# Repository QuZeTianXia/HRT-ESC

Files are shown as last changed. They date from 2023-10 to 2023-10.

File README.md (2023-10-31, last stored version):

# 更新日志      
(https://img.tg/image/O1jPRb)   
+2023/10/31/20:21   
赛前能用的四轮加压版本，但后轮还是会跳动，而且加压速率较慢。 
+ 2023/10/15/9:35  
梳理了逻辑，增加了使用CAN改变加压力度配制参数的功能。  
	+ Data[0] = 0xAA ---> Data[1] = Quick_Accelerate;  
	+ Data[0] = 0xBB ---> Data[1] = Slow_Accelerate;   
下一步计划增加P控制
+ 2023/10/13/21:34  
更新了23D四轮制动的版本，但未经测试。
+ 2023/10/13/21:25   
更新了23D刚刚可用的只有前轮制动的版本。

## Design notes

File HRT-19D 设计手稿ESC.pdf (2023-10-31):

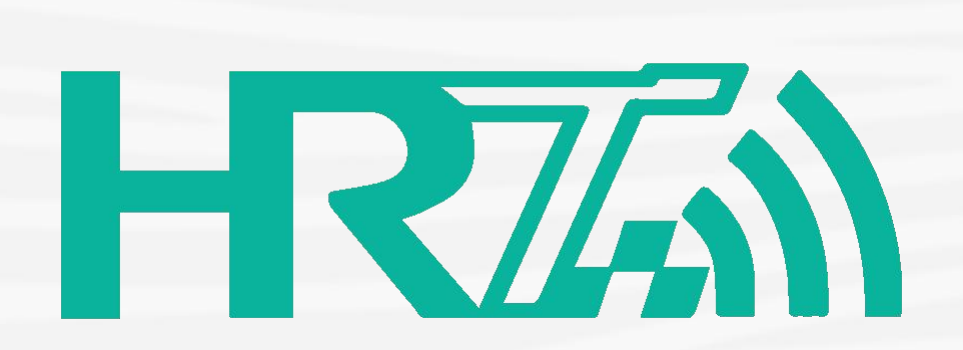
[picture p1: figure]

## Season 2019

## ESC 设计手稿

## Department of ESC

## 设计者： 卢奇麟 王书鹏 赵砚秋 等

## Designer: Qilin Lu、Shupeng Wang、Qiuyan Zhaoetc. 关键词： 稳定、快速响应、轻量化

## Keywords: Reliable, Rapid response, Light-weight

目录

## 1. ESC 功能

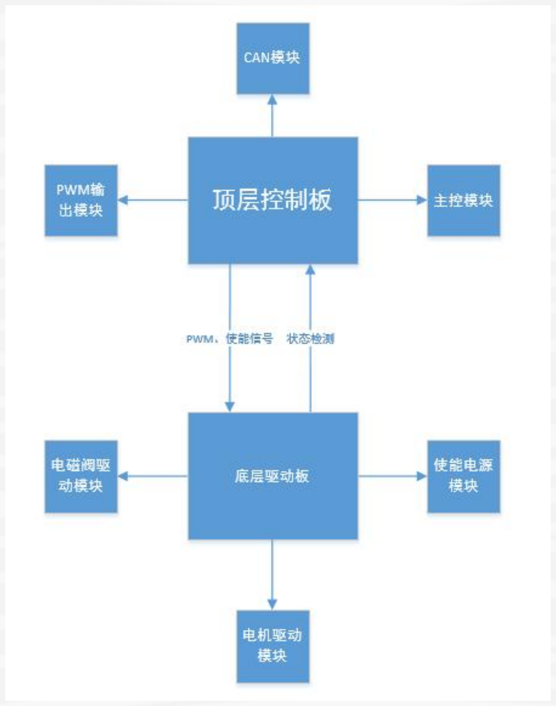
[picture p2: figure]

图 1-1 ESC 功能模块构成
ESC 全名为 Electronic Stability Control，一般用于控制车身高速行驶状态下的的稳定性。 今年车队研发 ESC 主要用于制动，实现对四个车轮稳定而准确可控的油压控制。
如图 1-1 所示，ESC 主要由两个部分构成：底层的驱动板以及顶层的控制板。其中顶层 控制板涉及到收发 CAN 信号，主控算法以及 PWM 输出三大部分；底层的驱动板主要涉及电 磁阀，电机的驱动以及电源使能模块，这些部分会在后文详细介绍。
由于 ESC 制动力不足，并不适合用于紧急制动，所以在功能上只是作为制动的冗余系统 以及检测系统，在进入 AS Ready 前以及实际 EBS 制动时检测油压，如果油压没有在规定时 间内（3s）增长到一定程度，就认为 EBS 错误，自动制动并发出代表错误的信号。另外在无 人跑动直线时，车辆需要缓停，制动力也由 ESC 提供。

## 2. 针对规则

3.2.4. 在 AS 切换至“AS Ready”前，必须存在一个初始状态检查来保证 EBS 和它的冗余系 统可以像期望的一样建立制动压力。
3.2.5. 驱动系统不被认为成制动系统。
3.2.6. 如果确保存在双向监测，行车制动可以认为是一套冗余系统。

## 3. 关联信号模块

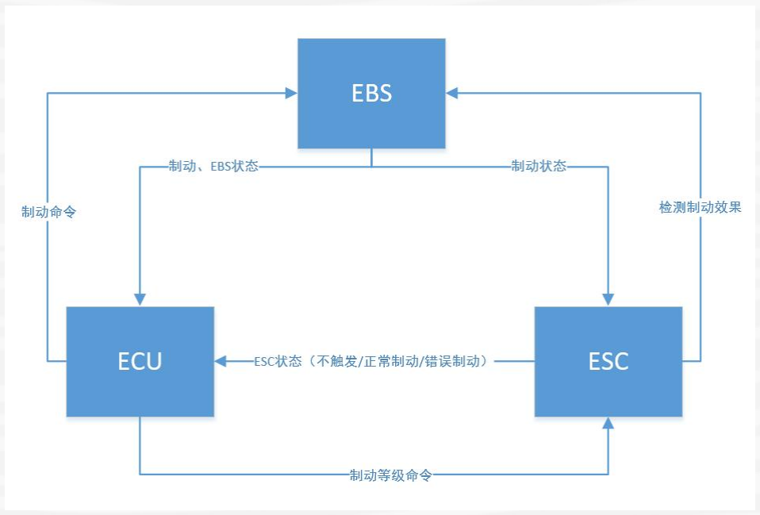
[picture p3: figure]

图 3-1 ESC 与整车信号交流示意图

如图 3-1 所示，ESC 主要与 EBS 和 ECU 有信号交流。其中 ECU 会向 ESC 发送 0-5 的制动 等级信号，分别对应油压 0 到 1Mpa。接收信号后，ESC 内部自带的电机转动（占空比 0.6-0。 9），并通过开闭电磁阀实现油路转换与油压调节，确保目标油压可以保持在一定范围内。同 时 ESC 也会自检油压，并发送自身的状态位。
ESC 会接收 EBS 的制动状态，并检测 EBS 是否正常制动。如果 EBS 制动后规定时间内没 有足够的油压，ESC 会自动补位，同时发送 EBS 的错误位。该错误状态会被锁存直到检测到 EBS 的状态不再是制动状态。
进入 AS Ready 状态前，ESC 会先进行制动，检测油压正常后，进入无人模式，EBS 触发。 如果 ESC 检测正常，则可以进入 AS Ready 状态，否则 ESC 报错，系统退出 AS Ready 状态。

## 4. 最终电路设计

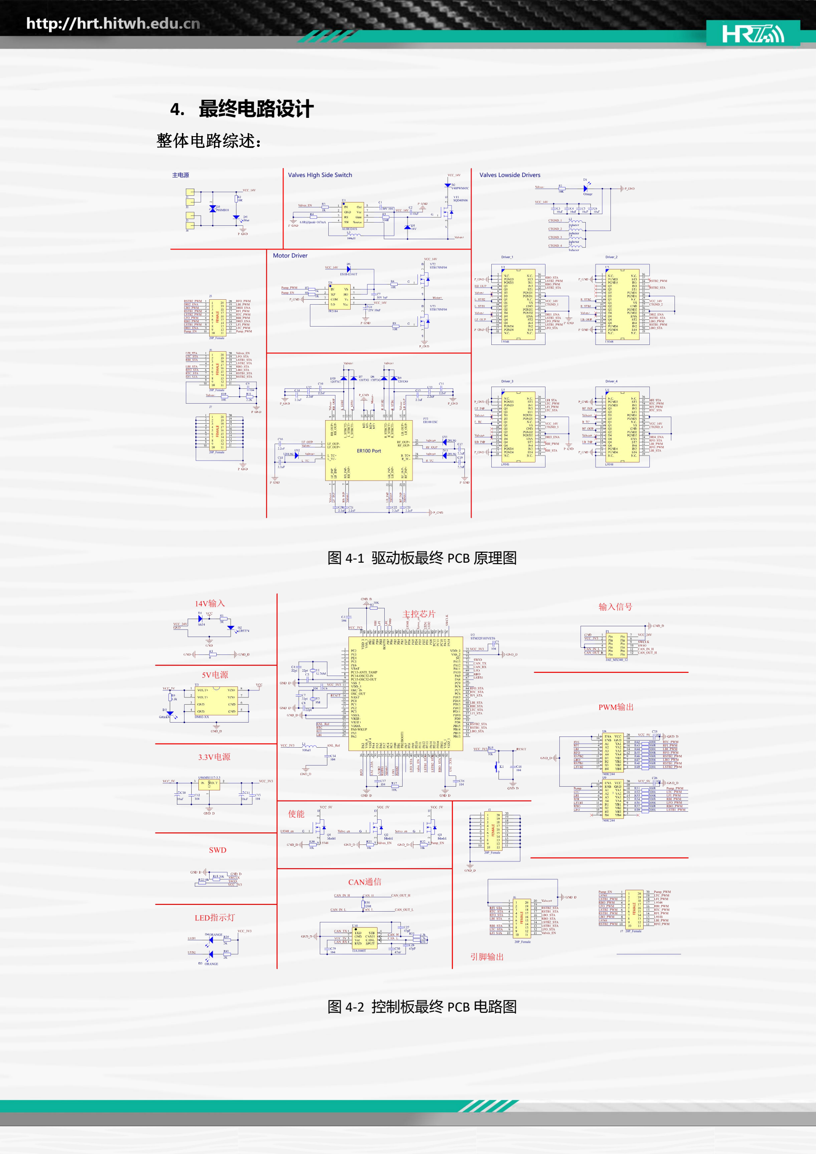
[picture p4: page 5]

整体电路综述：

图 4-1 驱动板最终 PCB 原理图

图 4-2 控制板最终 PCB 电路图

接下来介绍两个板子的主要构成部分，至于 LED、SWD 等不再赘述。 驱动板：

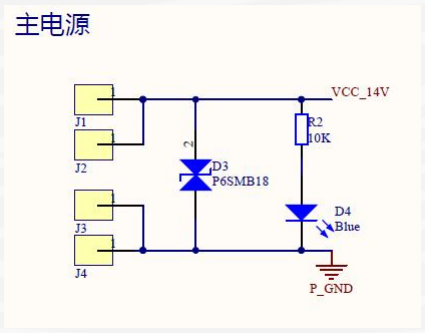
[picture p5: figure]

图 4-3 电源输入
由于电机的额定电压在 14V,为了避免电压过高损坏电机的问题，采用铝壳电源将低压 电 24V 转化为 14V 电源，驱动电机及电磁阀。该电流最大时可达 9A,铝壳电源最大电流 13A， 符合要求。
电路在接通、断开电感负载或大型负载时常常会产生很高的操作过电压，这种瞬时过电 压称为浪涌电压，是一种瞬变干扰。而电磁阀和电机都是大功率电感元件，在通断过程中即 便采用二级管泄压，难免会产生瞬时的过电压。P6SMB18 是一种双向瞬态二极管，在电压 超过 16.2V 时，可以瞬时导通以避免该部分电流损坏电路系统。

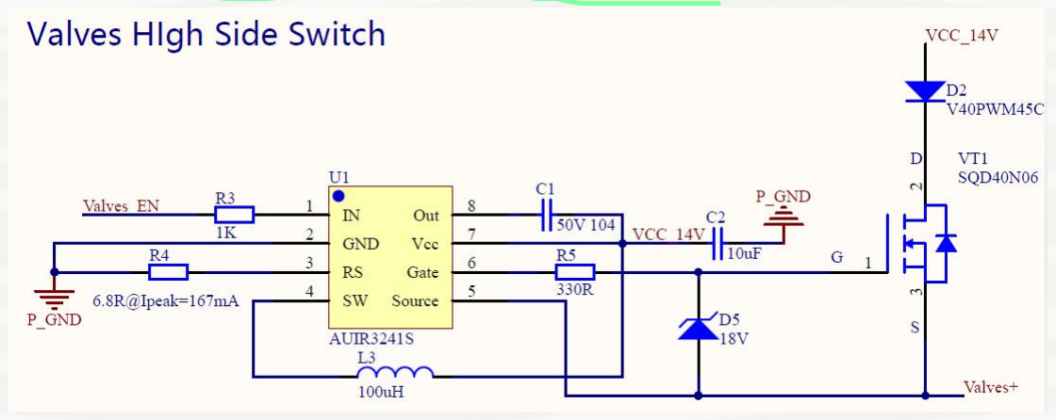
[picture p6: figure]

图 4-4 驱动板电源使能
该应用电路通过输入引脚 IN 实现对 Gate 开关的控制，进而控制整个电源的通断。 AUIR3241 是宽电压供电的大功率电源控制芯片，其供电电压可以为 3-36V 的任意值， 输入端的电压可以在 2.5-5V 之间实现整个电源电路的通断，可以兼容单片机 3.3V。 使用大功率 mos 管 SQD40N06 流经所有的电源电压,可承受 40A 的电流，完全符合系统的 要求(电磁阀部分最大约 6A)。

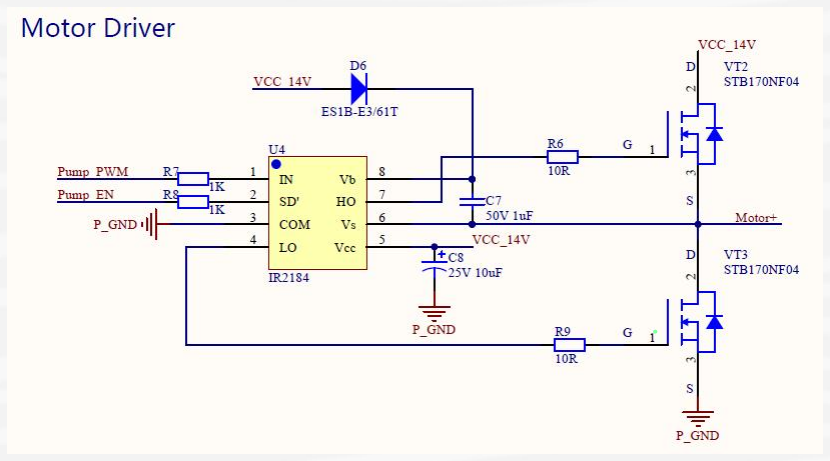
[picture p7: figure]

图 4-5 电机控制电路
该电路用于控制电机的停转。由于电机属于感性负载，其上的电流不能突变，不能直接 使用 PWM 控制二极管通断供电。IR184 是一种半桥功率放大芯片，可以通过两路相反的输 出分别控制电源和 GND 的通断，从而实现 PWM 直接控制电机的功能。
IR2184 的输入部分包括使能和 PWM。使能信号为低时，输出部分 HO 与 LO 都为低；否 则根据 IN 引脚的输入，HO 与 LO 输出相反。驱动电机的部分为典型的自举电路：IN 输入为 低时，LO 为高，Motor 和 GND 导通，此时电容 C7 由电源电压开始充电；IN 输入为高时， LO 为低，HO 的电压等于 Vb 的电压。MOS 管在 Vgs 达到一定压差时才会导通，因此 HO 与 Motor 上的压差等于电容电压，Motor 此时为高。如此充放电周而复始，实现 PWM 控制电 机转动的目的。
在实际测试的过程中，1uF 的电容在 PWM 频率为 1000HZ，占空比 0.7 时由于存储的电 荷不足，mos 管的 Vgs 达不到阈值，电机直接连接到 Vs 引脚。由于电机的电流不能突变， 过剩的电流击穿了 Vs 与 HO 之间的 mos 管，芯片损坏，后来换成 10uF 的电容，不再出现芯 片损坏的问题。

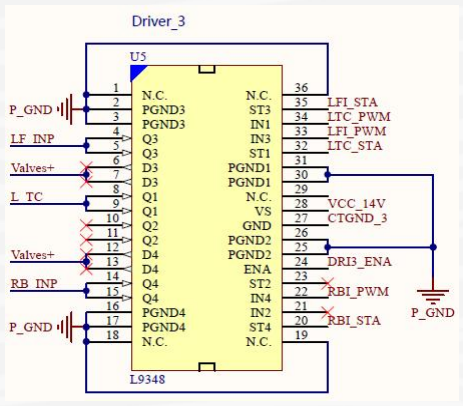
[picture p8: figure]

图 4-6 电磁阀驱动电路（一）

如图 4-6，电磁阀驱动电路使用 L9348 芯片，每一个芯片可以分别输出四路独立的 PWM，对应四个电磁阀开关控制。实际电磁阀数量为 14 个，共使用 4 个 L9348 芯片。 L9348 芯片包含四个输入端，4 个状态输出端，4 个电流输出状态（高阻态或导通）， 以及一个总的使能引脚。为了避免麻烦，控制板使用一个引脚控制 4 个芯片的使能。 L9348 本身不具有带动感性负载的能力，但支持 PWM 形式的高速通断，以及最大 3A 的电流导通，相比 1A 可以实现功能的电磁阀，电流输出要求可以满足。此外，该芯片可以 检测错误状态，包括输出过载、过温等。输出脚和输入脚在正常情况下会保持一致，（超过 667Hz 的输入会导致输出一直为高），发生错误后状态反转，所以可以输出电流时检测输出 状态，为低时报错。
另外，每个芯片的 VCC 和 GND 都有电容和电感滤波，不再单独截图。

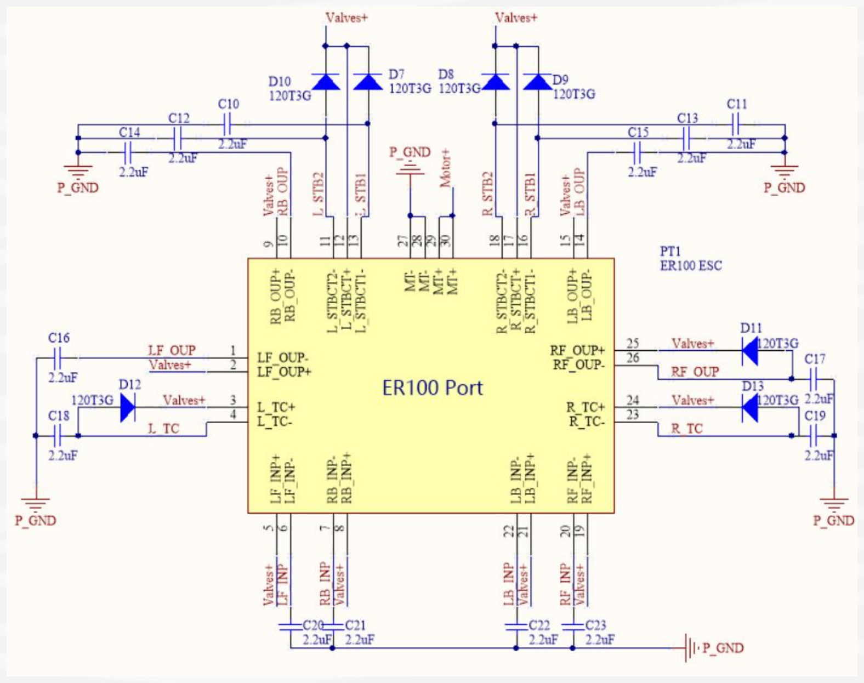
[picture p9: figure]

图 4-7 电磁阀驱动电路（二）

ER100Port 实际代表与电磁阀位置对应的过孔，实际通过焊线连接二者。L9348 的输出 代表与地导通与否，因此在导通且电源使能后，可以控制 PWM 形式的电流流过电磁阀，从 而控制电磁阀导通与否。
120T3G 是一种快速恢复整流二极管，适合实现高频下的通断。PWM 控制电磁阀时，由 于电磁阀为感性负载，其上电流不能突变，这部分电流经过 123T3G 二极管进入 Valve 电源 端，避免损伤 L9348 芯片。

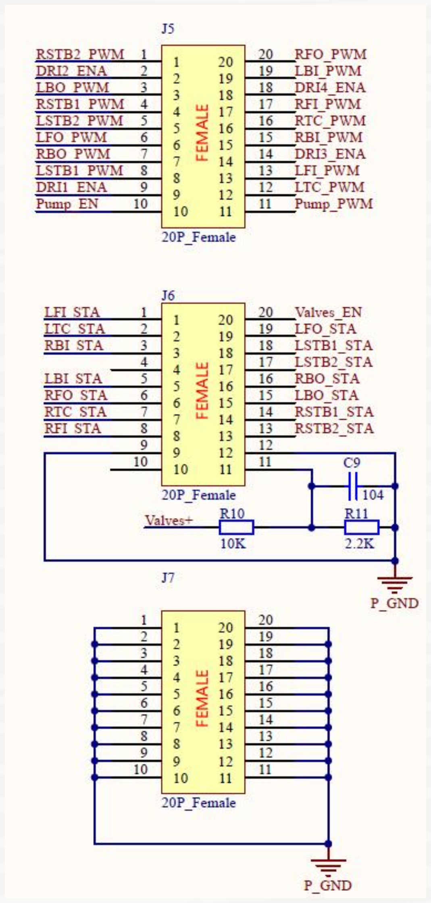
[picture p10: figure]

图 4-8 驱动板控制板连接

使用 Female 板对板连接器连接驱动板与控制板，同时固定二者之间的位置。信号包含 15 路 PWM，4 个 L9348 使能信号，1 个电机使能信号，1 个电源使能信号，1 个电源 ADC 信号采集口，以及 14 个状态位。

控制板：

控制板主要实现接收信号、中央控制、PWM 算法三个部分。

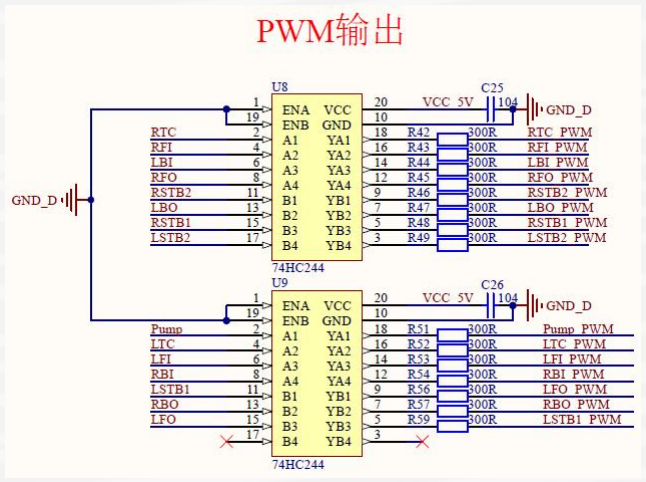
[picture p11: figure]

图 4-9 PWM 输出

一共有 14 个需要控制的电磁阀，再加上电机，实际共输出 15 路 PWM，分别由 4 路定 时器输出 PWM 。

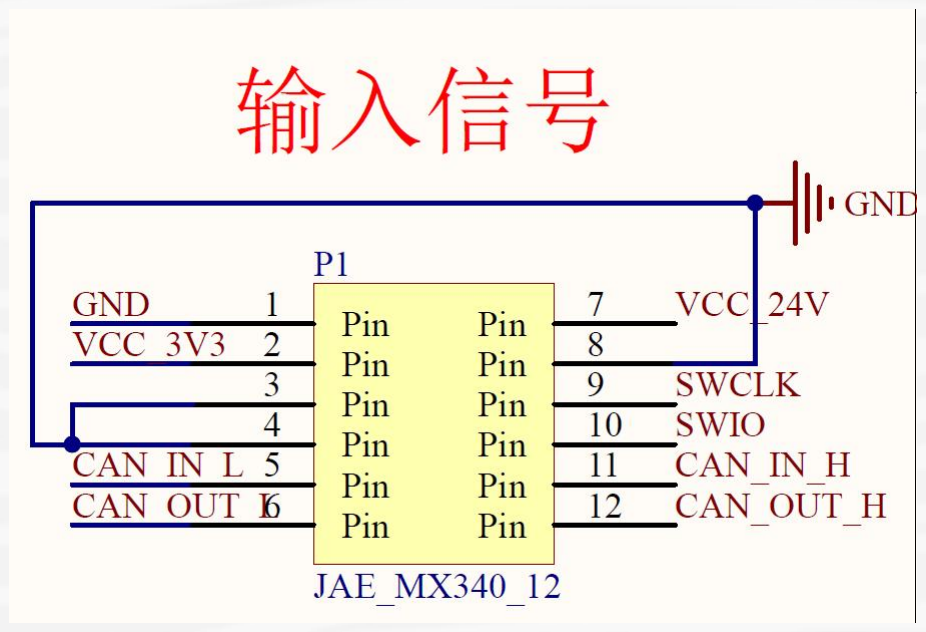
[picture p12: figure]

图 4-10 控制板的输入信号

输入信号较少，只有电源、CAN、SWD 下载口三个部分，获取整车状态以及和 EBS 双向通信都通过 CAN 通信。

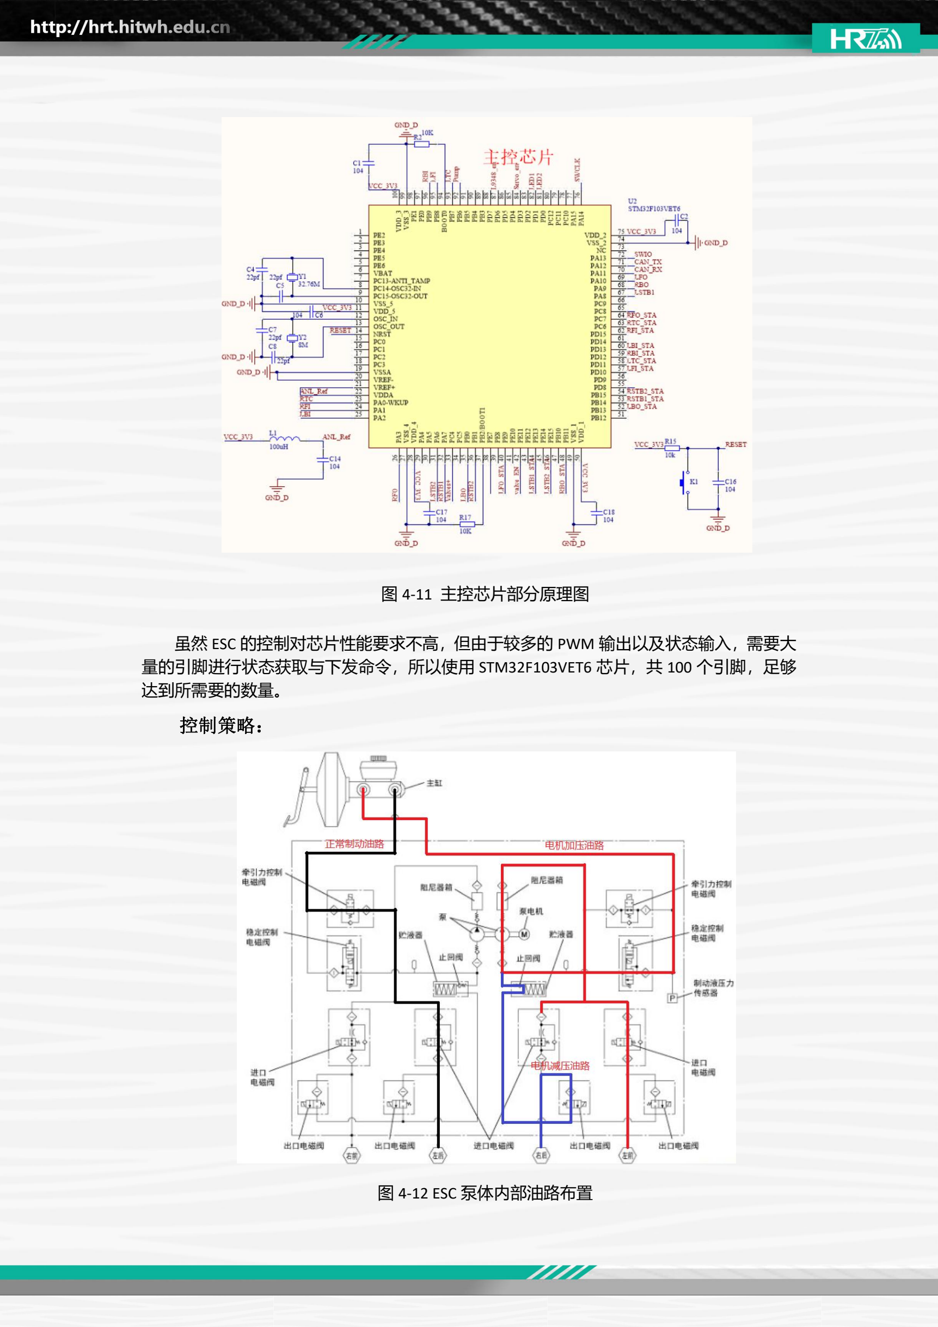
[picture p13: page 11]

图 4-11 主控芯片部分原理图

虽然 ESC 的控制对芯片性能要求不高，但由于较多的 PWM 输出以及状态输入，需要大 量的引脚进行状态获取与下发命令，所以使用 STM32F103VET6 芯片，共 100 个引脚，足够 达到所需要的数量。 控制策略：

图 4-12 ESC 泵体内部油路布置

| 进口电磁阀 | 出口电磁阀 | 牵引力控制电 磁阀 | 稳定性控制 电磁阀 | 电机
增压 | 不通电/ON | 不通电/OFF | 通电/ON | 通电/OFF | 转
降压 | 通电/OFF | 通电/ON | 不通电/OFF | 不通电/ON | 转
保压 | 通电/OFF | 不通电/OFF | 不通电/OFF | 不通电/ON | 不转
表 4-1 不同功能下电磁阀通断情况
如图 4-12 所示，ESC 使用电机进行加减压的过程实际就是改变制动油流动的路径以及电 机转动的 PWM 占空比。通过控制板输出 PWM 可以改变电磁阀开关状态，进而实现改变油 路的目的。
表 4-1 是具体实现修改油路的电磁阀通断表。当所有的电磁阀都不通电时，有人状态可 以正常的踩动加压，其油路由图 4-10 黑色线所示；要实现某一路增压，需要通电牵引力电 磁阀与稳定控制电磁阀，油路为图 4-10 的红色线所示，电机转动即可带动制动油流向轮边； 需要减压时，通电进口电磁阀与出口电磁阀，制动油沿着图 4-10 蓝线所示到达储液器；要 实现保压的目的，只需要通电进口电磁阀即可。
实际测试过程中发现，进口电磁阀可以基本保证油压不增加，但存在漏油现象，为了减 小该现象，实际控制时电机一直处于转动状态，也可以避免电机频繁停转对系统的冲击。

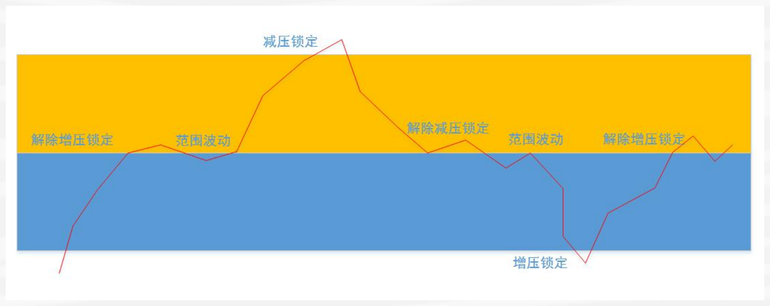
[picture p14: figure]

图 4-13 控制策略示意图
相比机械式的气瓶制动，ESC 的制动力明显不足，最大约 1MPa，不可能实现制动测试。 但 ESC 的优势在于可以实时监测控制各个车轮的油压，以达到制动力最优分配的目的。 ESC 控制油压时，系统总处于加压、减压、保压之一的状态，而状态之间切换的过程需 要一定时间并产生峰值电压，对系统不利。所以基本的控制策略如图 4-13 所示，分别设定 一个合适的上下阈值（中间值为目标油压），检测到油压波动超过设定的范围后，设置锁存 位，系统进入加压或降压的状态直到油压重新回到目标值。 实际测试时，关闭进口电磁阀油压整体有下降的趋势；为了避免测量油压时数据波动导 致的频繁状态转换，上下阈值必须选取与目标值相差较大；但选取过大的偏差，ESC 分配油 压的功能也就失去了意义。经过实际验证，0.08MPa 的阈值偏差为比较好的值。

控制流程

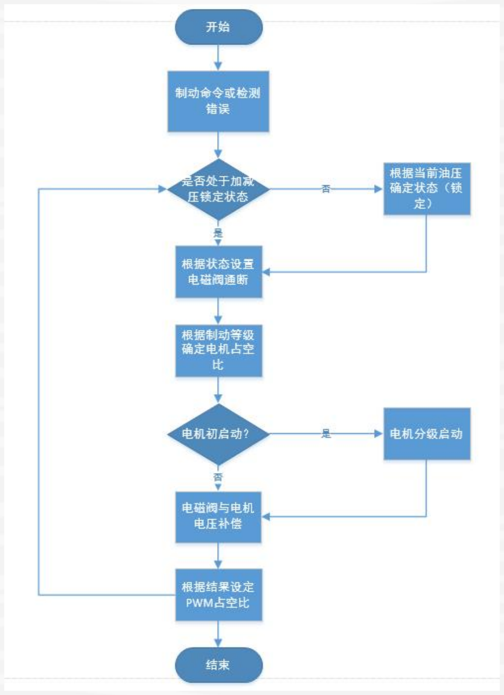
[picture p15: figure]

图 4-14 控制流程示意图

ESC 只在接收到制动命令或者检测到 EBS 制动错误后才会进入制动状态，制动状态控制 流程如图 4-14 所示。进入制动状态后，系统根据置位确定当前的锁定状态，如果没有，则 根据油压和目标值的差确定状态。进入锁定状态后（锁定加压、锁定减压），直到重新达到 目标油压才会停止。
电机的占空比依靠制动等级确定，一般要求电机直接加压时的油压大于目标油压。实际 控制时设定电机与制动等级线性相关，即 1-5 的制动等级对应 0.55-0.95 的电机占空比。 电机的电流与转速关系如下所示：

# Ua = Ce ∗ ∅ ∗ n + I ∗ Ra

所以电机通电时初始转速为零，与之对应的的电流等于 U/R。经过测量，R=3 欧，所以 电机初始启动时的电流非常大，对整个供电系统以及电机都有损害。采取分级启动的方法可 以减小大电流的冲击，即电机刚上电的 1s 内，设定占空比为 0.5+0.5*k（k 为制动等级），待 到电机转速达到一等程度后，再设定目标占空比，可以减小流经电机的冲击电流。 电压补偿可以确保实际的电流（电压/电阻）达到预定值。由于电磁阀（1A）与电机（约 3A）都是比较大电流的器件，难免在电流变化或总量较大时出现电源电压被拉低的情况。 所以需要实时检测电源电压，并根据实际电压按比例补偿占空比，确保电磁阀与电机的实际 电压达到预定值。
控制时序如表 4-2 所示：
Count | ECU | ESC | ESC | 油压采集板
0 | 制动命令 | | | 油压数据
1 | | 设定 PWM | 发送制动状态
2 | | | | 油压数据
3 | 制动命令
4 | | 设定 PWM | 发送制动状态 | 油压数据
5
6 | 制动命令 | | | 油压数据
7 | | 设定 PWM | 发送制动状态
8 | | | | 油压数据
9 | 制动命令
10 | | 设定 PWM | 发送制动状态 | 油压数据
11
12 | 制动命令 | | | 油压数据
13 | | 设定 PWM | 发送制动状态
14 | | | | 油压数据
15 | 制动命令
16 | | 设定 PWM | 发送制动状态 | 油压数据
17
18 | 制动命令 | | | 油压数据
19 | | 设定 PWM | 发送制动状态
20 | | | | 油压数据
30Hz | 10Hz | 10Hz | 10Hz | 15Hz

ECU 以 10Hz 的频率发送制动命令，ESC 也以 10Hz 的频率计算设定 PWM 占空比； 而油压采集信号以 15Hz 的频率获得，高于 ESC 的控制频率，避免数据未更新导致的控制 问题。
油压采集板由一个单独的板子采集，并通过 CAN 信号将采集到的油压发出来。油压采 集板实质为 4 路 ADC 采集板，这里不再赘述。采集到的数据不经处理，以 8 个 CAN 位发 送，每一路油压共 12 位，ESC 需要进行解码获得实际数据。

控制效果

## 5. 传感器选型

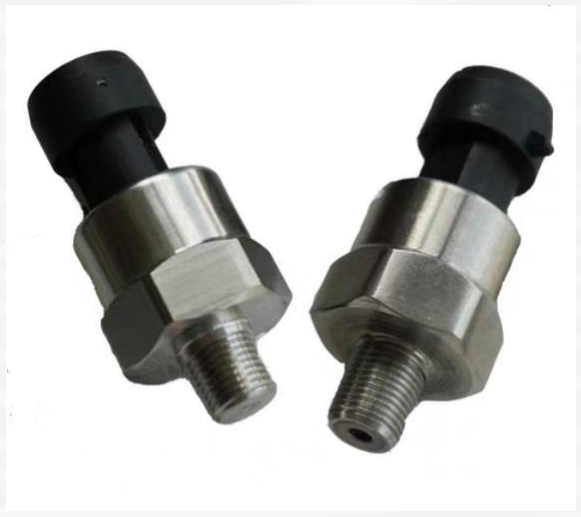
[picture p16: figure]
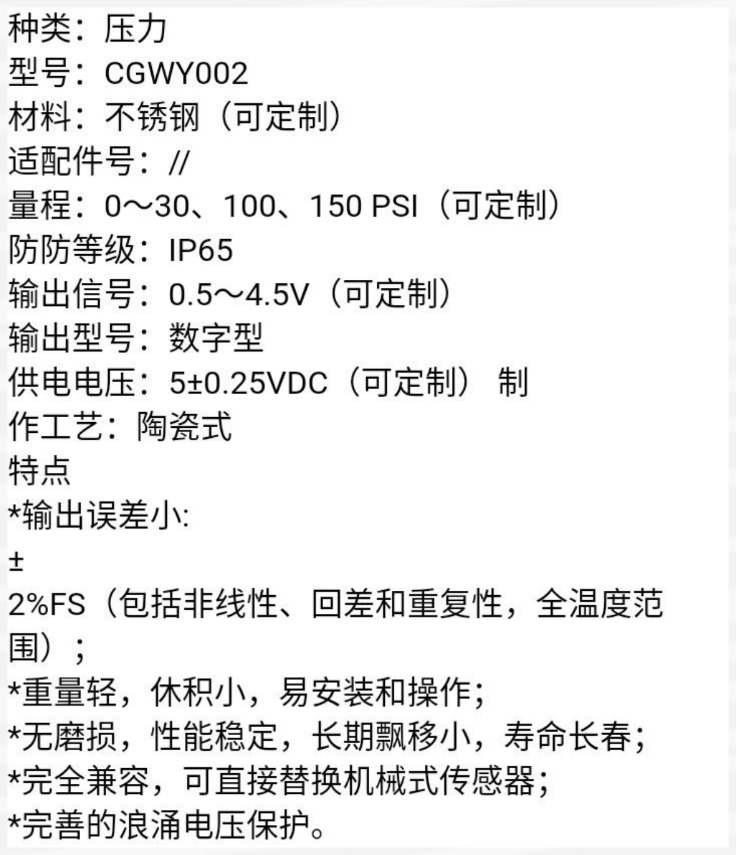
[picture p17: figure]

图 5-1 油压传感器型号

油压传感器定制型号 5V 供电，0.5-4.5V 输出，8MPa 的最大压强测量范围，足够赛车车 轮抱死的油压。

## 6. 安装位置

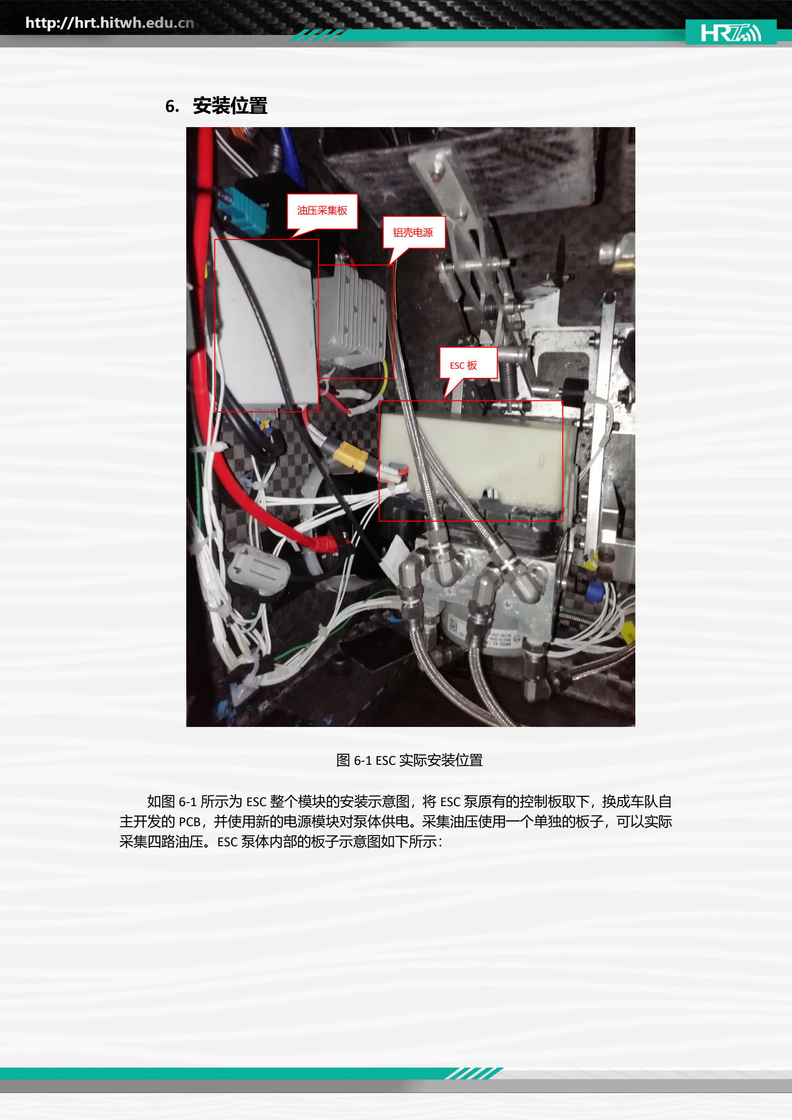
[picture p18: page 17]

图 6-1 ESC 实际安装位置

如图 6-1 所示为 ESC 整个模块的安装示意图，将 ESC 泵原有的控制板取下，换成车队自 主开发的 PCB，并使用新的电源模块对泵体供电。采集油压使用一个单独的板子，可以实际 采集四路油压。ESC 泵体内部的板子示意图如下所示：

铝壳电源

油压采集板

ESC 板

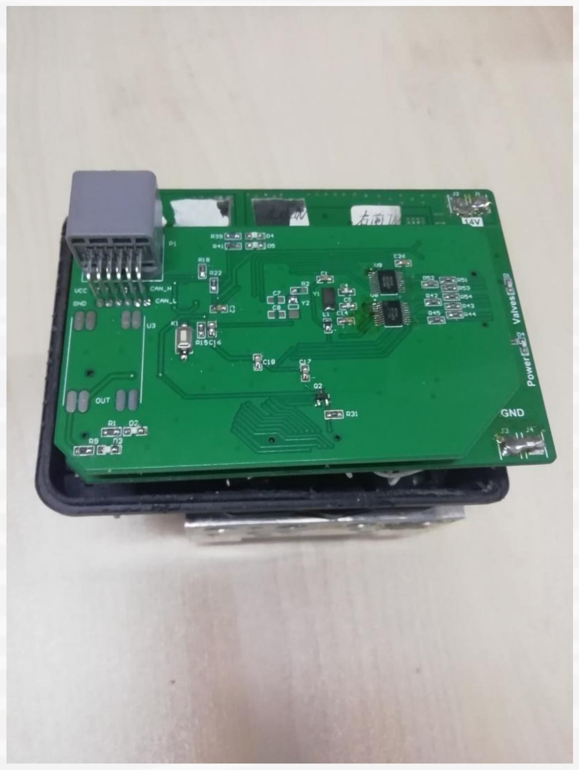
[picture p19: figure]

图 6-2 ESC 内部泵体安装示意图
驱动板与泵体之间通过 MX34 插头连接，电磁阀与电机的的引出脚使用线束焊接，外包 绝缘胶带，再用热熔胶糊上以避免短路。驱动板与控制板之间通过 Female 板对板连接器连 接，在使用热熔胶固定，确保不出现连接松动问题。

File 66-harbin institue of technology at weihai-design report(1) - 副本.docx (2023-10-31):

写在最前面（记得删除）

此为设计手稿模板

今年的模板一是在静态赛答辩时如有需要可以给裁判查阅；二是中国赛或德国赛的设计报告我需要参考每一个系统的设计手稿来写；三是尽可能写的详细些以便后续学弟学妹们关于设计有据可查，不要再发生连着几年设计报告长一样的事情了。

今年因为需要参加国外比赛，所有的内容必须中英文对照，中文在前，英文在后。目录因为word本身的问题所以只能中文/English。

我列的模板大多是以底盘为基本思路，其他系统可以按照自己的设计流程来修改，记得把目录的编号整理好并且及时更新目录

标题和文本的字体已经在模板里列出。

另外关于内容，还是想提醒一下大家多考虑考虑每一个和自己配合或者配合对方的系统，比如悬架要如何考虑空套，应该给空套什么样的设计指导，裁判很喜欢问这种问题

同时，国外有很多非常优秀的关于FSAE设计的论文，设计思路或者排版等都值得我们学习，很容易找到很多,我们也应当写成类似一篇论文的形式，直观

页眉页脚在发给大家的时候应该已经做好了

HRT-23E

Xxx系统设计报告

Design of the HRT-23E

XXXX

此处添加系统渲染图

系统：

Department:

设计人：

Designer:

序言

Introduction

# 1. xx系统设计依据/ Bases of the xx design

## 1.1xx系统总览/Overview of xx

### 1.1.1整体设计思路/Overall Design Mentality

正文中文部分字体使用宋体小四，1.25倍行距，首行缩进两字符。

The English part of the text uses the Times New Roman font, 小四, 1.25x line spacing，and the first line indented by two characters (the indentation setting is consistent with Chinese).

第二段内容[1]。（引用-交叉引用-选择引文-设置字体为上标）

Content of the second paragraph.

第三段内容[2]。

Content of the third paragraph.

思维导图：（此处插入思维图）

（系统内部应当有一份设计思路和流程，具体的各系统的整车设计目标之后会下发）

## 1.2整体设计目标/The Design Objective

（个人觉得1.2和1.3应该互换，这个看各系统自己了，如果说找不到对标的那就删了，但再怎么样至少也得和自己对个标吧。。。）

## 1.3与往年本队和其他车队之间的比较/Comparison with other cars

# 2.xx整体结构设计

## 2.1几何设计

## 2.2仿真

## 2.3优化

# 3.xx系统实验与测试/Experiment & Tests

## 3.1xx零部件实验与仿真/

### 3.1.1目的/Purpose

### 3.1.2方案/Solution

### 3.1.3流程/Procedure

### 3.1.3结果及其分析/Result and Analysis

## 3.2实车测试/Vehicle Test

### 3.2.1数据采集/Data Collection

### 3.2.1实车与仿真数据对比/Comparison of Real Car and Simulation Data

### 3.2.3实验结论/Experiment Conclusion

# 结论/Conclusion

# 缩写与符号/Abbreviation and Symbols

Ax [G] 纵向加速度/Longitudinal acceleration

V [m/s] 速度/Velocity

（因为国内外使用的部分单位不一样，加上给后续学弟学妹能完全看懂，把缩写和符号的释义添加在此处，或不写在此处直接标注在公式下方）

# 附录/Attachment

（此处添加一些例如ansys静力学仿真分析，轮胎拟合的具体参数图，matlab程序等等，在正文中不太重要的内容的图片，如果裁判有兴趣再翻出来给他/她看）

66- Harbin Institute of Technology at Weihai Design Reporter-System Name-FSGE 2023

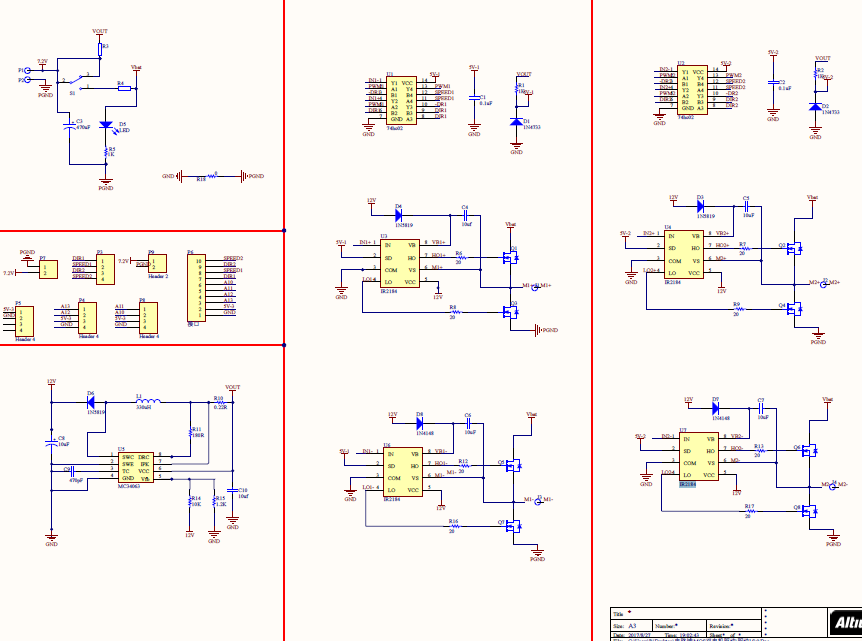
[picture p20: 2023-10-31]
电机驱动资料/IR2184/Fhp-q8nYSGP7Wf9nr_oFQut66e-g.png

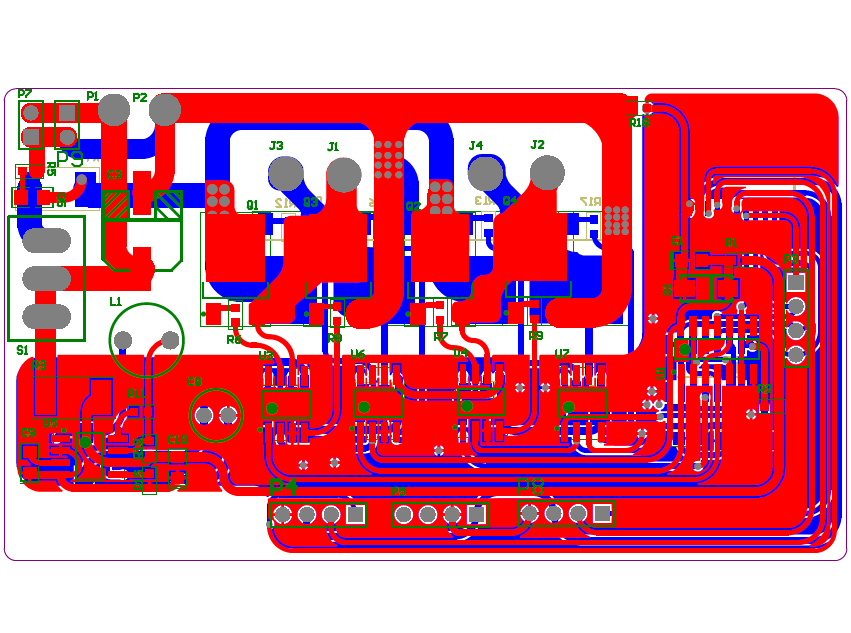
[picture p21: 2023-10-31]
电机驱动资料/IR2184/FrYy-v8_FWLyPjstqdibtAug80po.png

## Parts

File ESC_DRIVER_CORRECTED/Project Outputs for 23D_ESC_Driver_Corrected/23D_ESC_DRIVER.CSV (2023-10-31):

Bill of Material for
On 2023/9/10 at 14:09:01
Comment | Pattern | Quantity | Components
10K | R 0805 | 3 | R2, R9, R10 | 电阻
10R | R 0805 | 2 | R1, R8 | 电阻
10uF | C 0805 | 4 | C3, C5, C6, C7 | 无极性电容
120T3G | DO-214 | 14 | D8, D9, D11, D12, D13, D14, D16, D17, D18, D20, D21, D22, D24, D25 | 二极管
18V | LL34 | 1 | D5
1K | R 0805 | 3 | R3, R4, R5 | 电阻
2.2uF | C 0805 | 14 | C8, C9, C10, C11, C12, C13, C14, C15, C16, C17, C18, C19, C20, C21 | 无极性电容
2.54-1*20P直针 | HDR2.54-LI-20P | 1 | J7 | 排数:单排;总PIN位数:20;间距:2.54mm;插针结构:1x20P;行距:-;安装类型:直插;圆针/方针:方针;额定电流:3A;额定电压:-;配合针长度:-;塑高:-;端接针长度:-;触头材质:黄铜;触头镀层:-;工作温度范围:-40℃~+105℃;颜色:黑色;
2.54-1*20P直针 | HDR-TH_20P-P2.54-V-M-1 | 2 | J5, J6 | 排数:单排;总PIN位数:20;间距:2.54mm;插针结构:1x20P;行距:-;安装类型:直插;圆针/方针:方针;额定电流:3A;额定电压:-;配合针长度:-;塑高:-;端接针长度:-;触头材质:黄铜;触头镀层:-;工作温度范围:-40℃~+105℃;颜色:黑色;
25V 10uF | CP 3528B | 1 | C4 | 极性电容
330R | R 0805 | 1 | R7 | 电阻
50V 104 | C 0805 | 1 | C2 | 无极性电容
50V 10uF | C 0805 | 1 | C1 | 无极性电容
6.8R@Ipeak=167mA | R 0805 | 1 | R6 | 电阻
AUIR3241S | SOP8 | 1 | U2 | B2B MOSFET Driver
ES1B-E3/61T | DO-214 | 1 | D1 | 二极管
Inductor | L 0805 | 5 | L1, L2, L3, L4, L5 | 电感
IR2184 | SOP8 | 1 | U1 | Half-Bridge Gate Driver
MX34032NF2 | CONN-TH_MX34032NF2 | 1 | CN1 | 间距:2.2mm;插针结构:2x16P;排数:2;每排PIN数:16;行距:3mm;公母:公型插针;安装方式:弯插;
orange | LED_0805 | 2 | D6, D7 | 发光二极管
P6SMB18 | DO-214AA | 1 | D3 | BiDir TVS Diode
POWER_SO_20 | POWERSO-20_L15.9-W11.0-P1.27-LS14.2-BL-EP | 4 | 1, 2, 3, 4
RED | LED_0805 | 1 | D4 | 发光二极管
SMT_Connector | SMT_Connector | 4 | J1, J2, J3, J4 | 表贴接线端
SQD40N06 | TO252 | 1 | VT2
SQD40N06 | TO263-3B | 2 | VT1, VT3
SS34 | DO-214 | 4 | D10, D15, D19, D23 | 二极管
V40PWM45C | TO252_DIO | 1 | D2 | 二极管

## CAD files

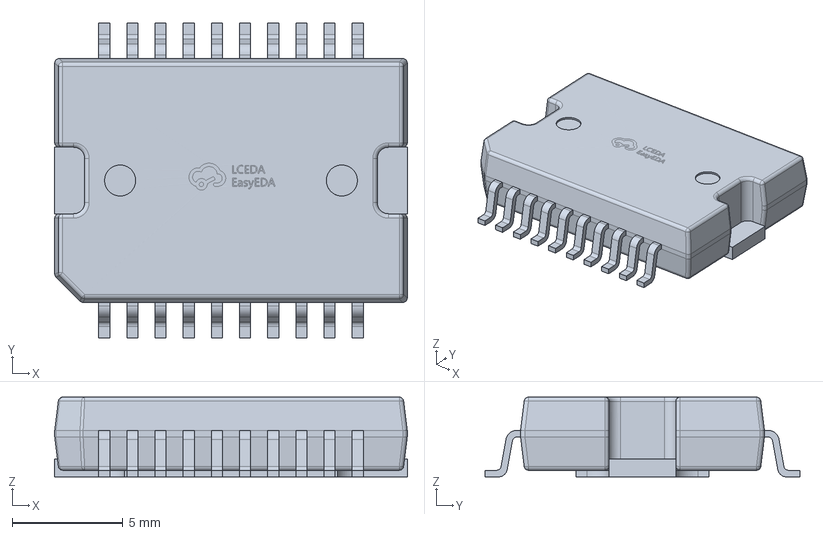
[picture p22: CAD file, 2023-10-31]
23D-ESC原理图+PCB/V3/23D_ESC_DRIVE/PowerSO-20_Library/3D_PCB3_2023-04-30.stp
15.9 x 14.2 x 3.60 mm

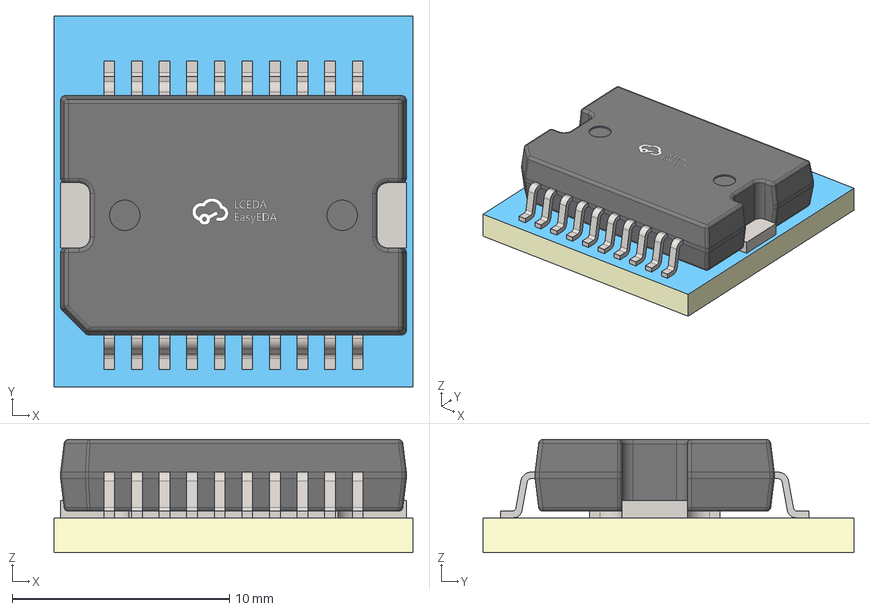
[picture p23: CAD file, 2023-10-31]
3D_PCB3_2023-04-30.step
16.5 x 17.1 x 5.20 mm

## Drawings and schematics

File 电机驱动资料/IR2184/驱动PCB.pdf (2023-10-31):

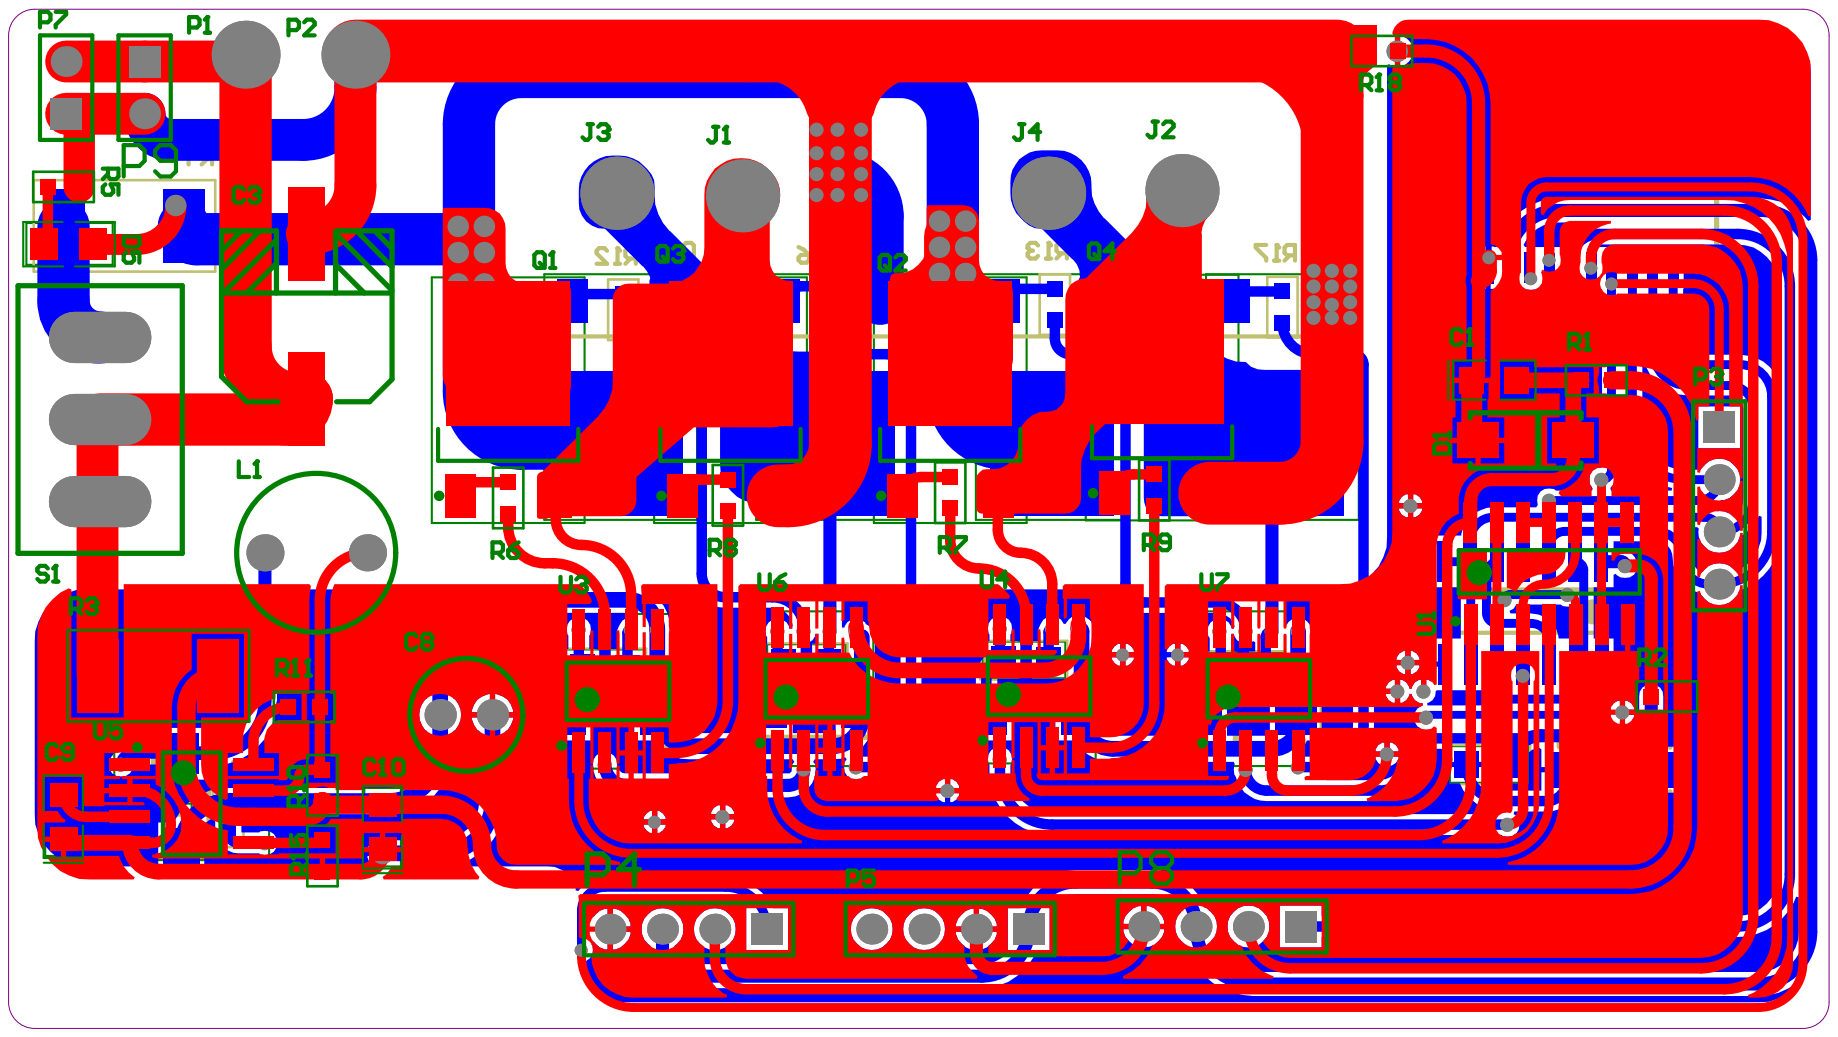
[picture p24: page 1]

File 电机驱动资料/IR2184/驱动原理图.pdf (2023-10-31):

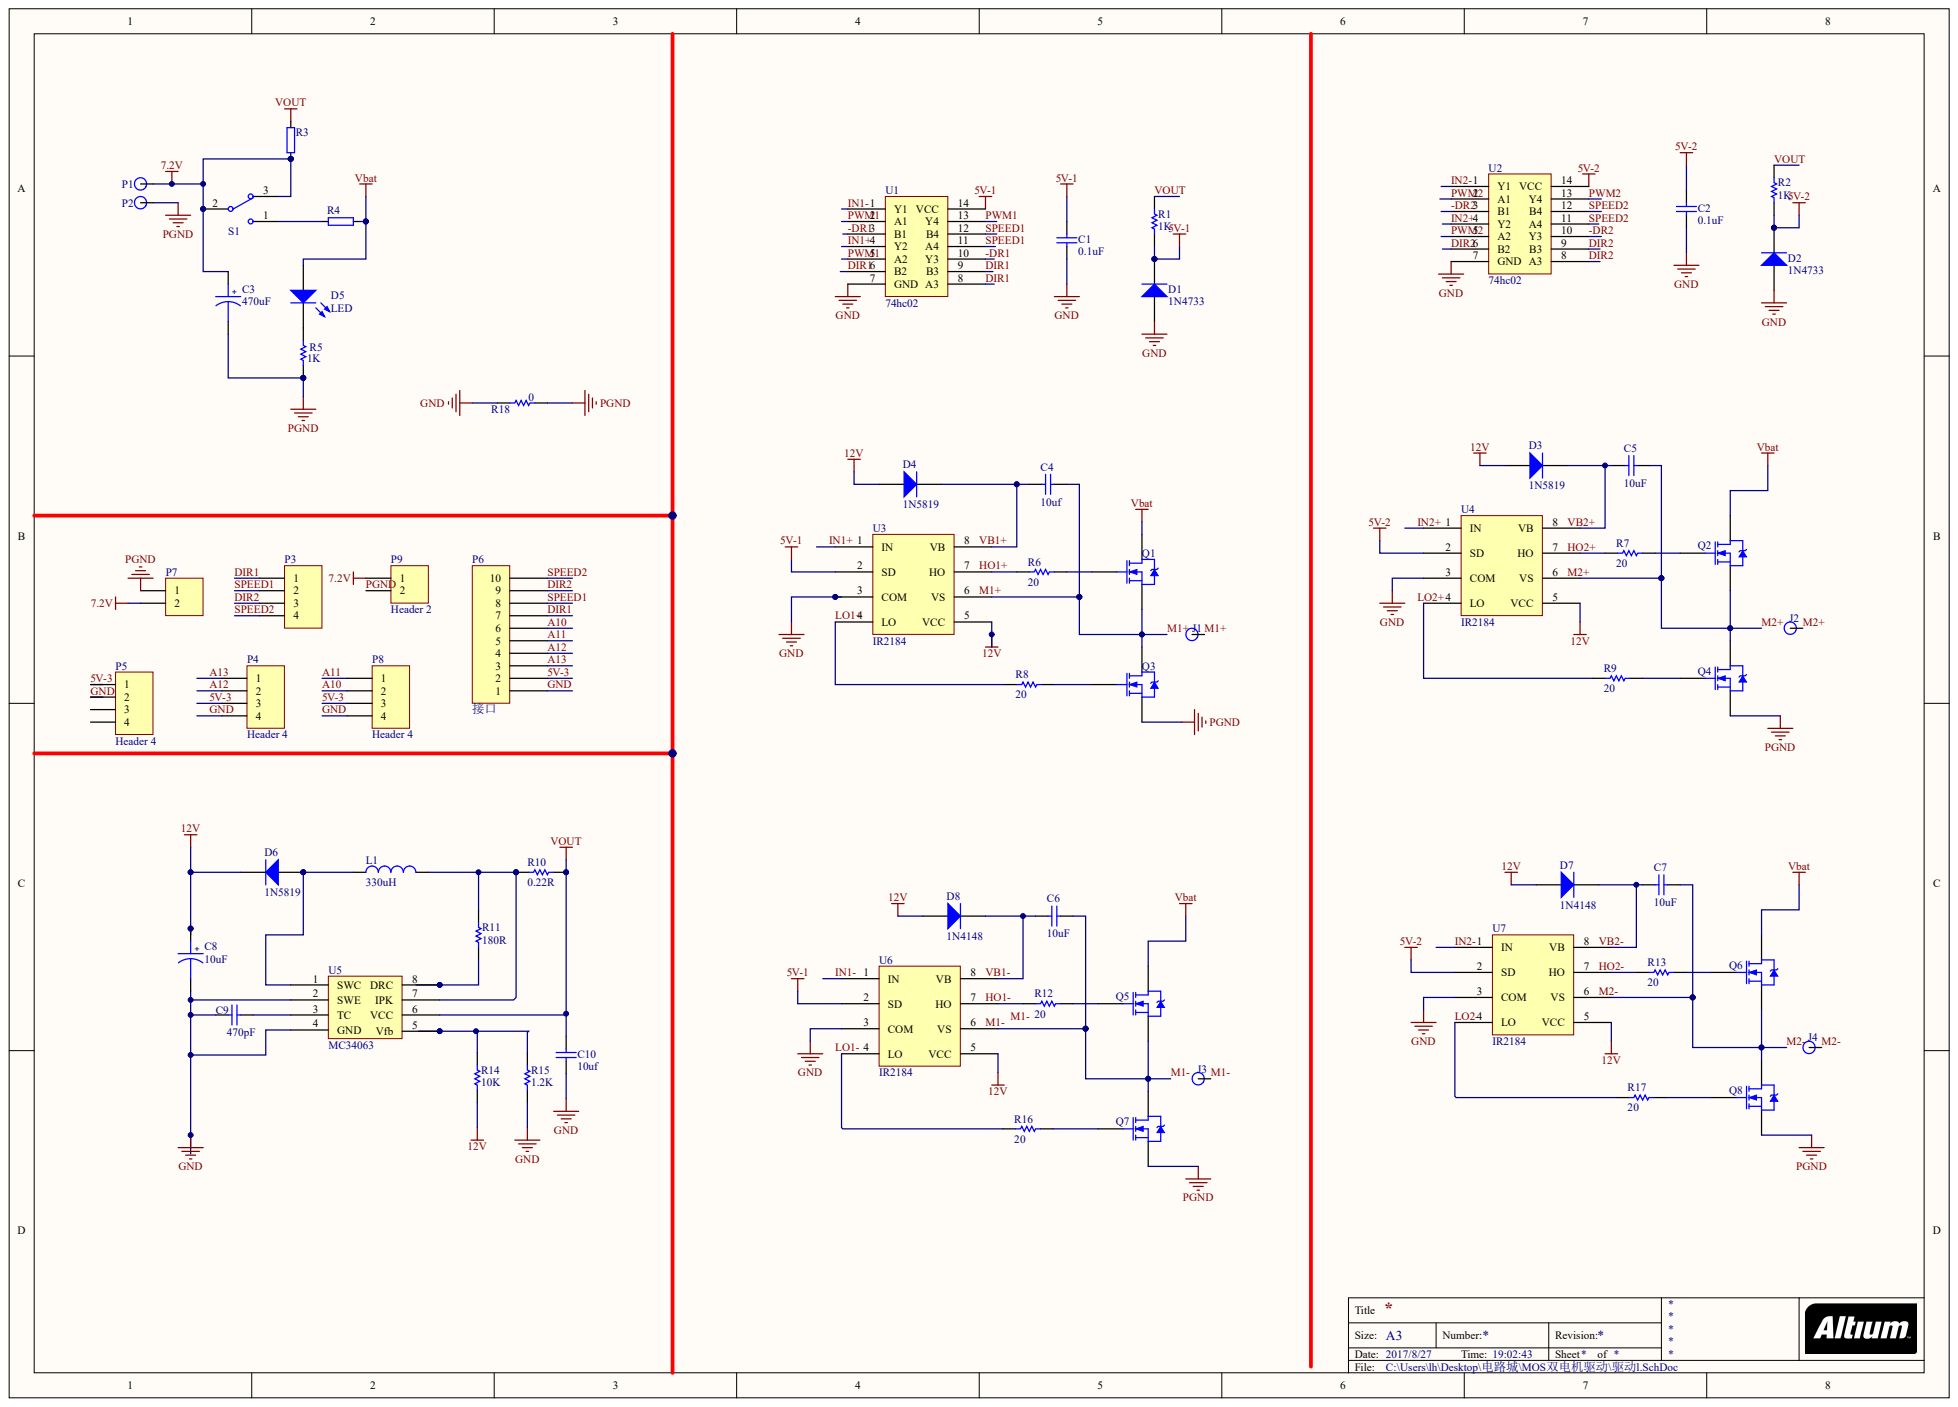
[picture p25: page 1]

* Title | **** *

Size: A3 | Number: * | Revision: *

Time: | | Sheet * of *
